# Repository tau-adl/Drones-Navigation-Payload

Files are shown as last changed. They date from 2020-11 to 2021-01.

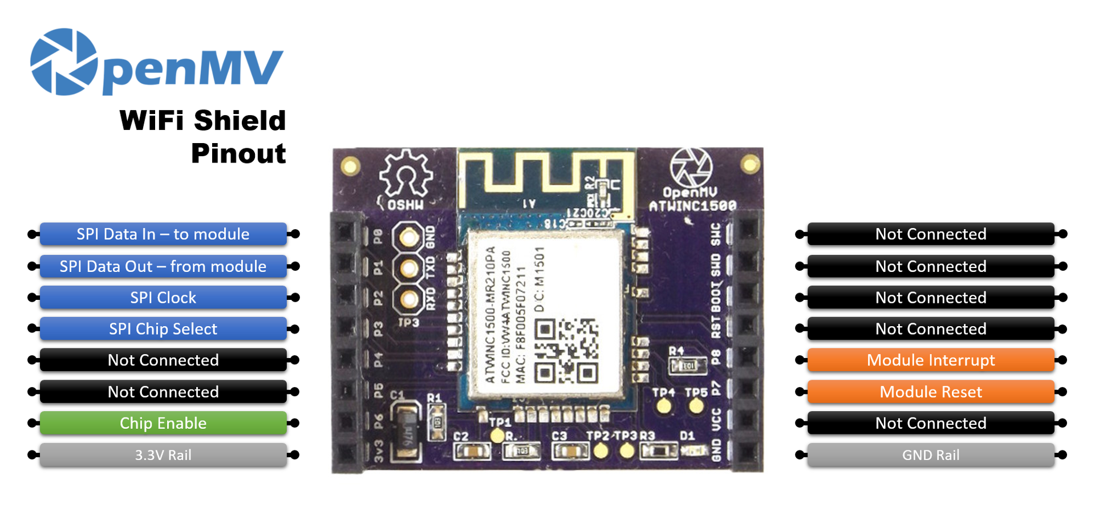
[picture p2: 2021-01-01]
datasheets/openmv/openmv-wifi-pinout.png

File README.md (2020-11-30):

# Drones-Navigation-Payload
The goal of the project is to build a payload taken by a drone that transmit both IMU and Images to a python script on a computer. 
Later, this information will be processed by ROS environment for navigation with SLAM algorithm. 

The Hardware for this project is based on the OpenMV(c) cH7 camera circuit loaded with global shutter camera, wifi shield and MPU6050 IMU sensor.

The repo cantains python script to be run as "ground-station" and the original firmware that runs on the main MCU.

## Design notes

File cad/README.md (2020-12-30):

# CAD files

## Hardware setup

## Dependencies

## Contributors and contributors
@Shenhavo
@danblana

case-r1.stl - OpenMV `https://github.com/openmv/openmv-boards/blob/master/cad/case-r1.stl`
OpenMV_Camera_Case - SteveTE `https://www.thingiverse.com/thing:1656029`

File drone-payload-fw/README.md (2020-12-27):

# drone-payload-fw

Project based on the OpenMV(c) firmware, modified to achieve real time image capturing and IMU data fusion, to be sent via Wifi to a  groundstation

## Hardware setup

** add circuit diagram **

|Part|OPENMV part|Model |
|--|--|--|
| MCU | OPENMVH7 | ST STM32H743 |
| Camera| OPENMV GS Camera  | ON MT9V034 |
| Wifi| OPENMV WifiShield | Atmel ATWINC1500 |
| IMU|  | Invensese MPU-6050 |
|Debugger/flasher||STlink V3|
|USB to UART|FTDI or similar|

## Debug info setup
uart @ baud = 115200.
win - `docklight` terminal or similar
ubuntu - `minicom`, `screen` or similar

# Defines and build configurations

- `camera_mngr.h` , frame size @  `FRAME_SIZE`,  `IMG_W`,  `IMG_H`
- `camera_mngr.h` , debug flags @  `CAMERA_BENCHMARK` - for printing acquisitions benchmarks,  `SAVE_INPUT_IMG_ON_SD`,  `SAVE_OUTPUT_IMG_ON_SD` - to save source and ouput images in SD card (~use carefully, it affects timings!)
- `main.h` - Wifi's SSID @ `MAIN_WLAN_SSID`

## Dependencies
STM32CubeIDE - Version: 1.4.2 - install from `https://www.st.com/en/development-tools/stm32cubeide.html`

## Contributors
@Shenhavo
@danblana

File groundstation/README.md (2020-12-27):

# groundstation

Ground station for `drone-payload-fw`
This code handles data comes from the drones payload, manages sockect and communication transactions utilizing proprietary protocol and exports the output on PC.

## Hardware setup

* wifi access
* drone payload with `drone-payload-fw` loaded
* tested on WIN10

## Dependencies
* numpy
* py-opencv
* opencv
* libopencv

if you use `ROS`
* ROS

## Contributors
@Shenhavo
@danblana

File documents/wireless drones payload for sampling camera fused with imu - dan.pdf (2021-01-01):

# אוניברסיטת תל אביב

הפקולטה להנדסת חשמל

## מטע"ד אלחוטי לרחפן לדגימת מצלמה וחיישן אינרציאלי בזמן אמת

## Real Time Wireless Drone’s Payload for

## Sampling Images and IMU data

פרויקט גמר לתואר שני בהנדסת חשמל

ע"י

# דן בלנארו

מנחה הפרויקט: מר יהונתן מנדל

המעבדה לרחפנים אוטונומיים באוניברסיטת תל-אביב

דצמבר 2020

## 1 תוכן עניינים

### 1 תוכן עניינים 2 |

### 1 מבוא 3 |

### 2 מטרות הפרויקט 4 |

### 3 איפיון דרישות המערכת 4 |

### 3.1 בחירת הרכיבים 4 | 3.2 סקר שוק 5 | 3.3 מצלמה6 | 3.4 חיישן IMU6 | 3.5 המודול האלחוטי 6 | 3.6 הבקר 7 | 3.7 חיבורים ואספקות מתחים 7 | 3.8 סקירת רכיבי הפרויקט 8 |

### 4 תכן מערכת 9 |

### 4.1 תרשים בלוקים: 9 |

10 | STMICRO STM32H743 - | הבקר | 4.2
11 | BOARD SUPPORT PACKAGE – GPIOS | והקצאת | BSP | 4.2.1
4.2.2 מפת חלוקת שעון מרכזי 13 |
4.2.3 פריפריות בשימוש 14 |
19 | ON SEMICONDUCTOR MT9V034 – | מצלמה | 4.3
20 | MICROCHIP ATSINC1500 - WIFI ה | מודול | 4.4
21 | INVENSENSE MPU6050 – IMU – | האינרציאלי | החיישן | 4.5

### 5.1 ארכיטקטורה 22 |

5.1.1 מבנה שכבות הקוד 22 |

### 5.2 תכנת תחנה קרקעית 25 | 5.3 ממשקי DEBUG, צריבה ושימוש במערכת 26 |

### 6.1 תצורת המדידה 27 | 6.2 תוצאות 27 |

### 7.1 סיכום 28 | 7.2 עבודות המשך 28 |

### 8.1 תמונת נוספות של המערכת 29 | 8.2 ביבליוגרפיה 30 |

## 1 מבוא

רחפנים כיום מנווטים באמצעות עיבוד החיישנים שמותקנים עליהם . אם עבור רחפנים בסביבות חיצוניות )outdoor ) משתמשים בחיישנים כגון GPS, הרי שלרחפנים בסביבות סגורות )Indoor )לא ניתן לשתמש בחיישן כזה.

הפרויקט עוסק במימוש מטע"ד )payload )אלחוטי וקומפקטי לרחפן, למטרות חישה ודגימה של רכיבים לטיוב הניווט באמצעות אלגוריתם SLAM.

לטובת הנ"ל, ניתן להשתמש בחיישני עזר נוספים, כגון מצלמה - להתמצאות במרחב, ובחיישנים אינרציאליים )IMU)- שיכול להשלים מידע לאלגוריתמי עיבוד תמונה בנוגע למהירות התנועה וקצב התנועה של הרחפן. באמצעות היתוך מידע בין 2 החיישנים, ניתן להשיג מידע חזותי-אינרציאלי ולבצע מיפוי והתמצאות של המרחב )SLAM(

]1[

רחפנים שמסוגלים לנווט בסביבה סגורה יכולים להביא תועלת רבה במקום שבה רחפנים לסביבות חיצוניות מביאים – לדוגמא ליישומי בנייה, חקלאות, רפואי, מסחרי, צבאי, קולנוע וגם לפנאי.

העבודה כאן מציגה שיתוף פעולה במעבדה לרחפנים אוטונומיים באוניברסיטת תל אביב ADL-TAU, על מנת לממש את מטרות הפרויקט
- סקר ספרות
- הבנת דרישות המערכת
- תכן על
- סקר שוק ובחירת רכיבים
- מימוש החומרה והתכנה לפרויקט
- חקר ביצועים
- סיכום

## 2 מטרות הפרויקט

הפרויקט יממש מערכת לחילוץ מידע חזותי-אינרציאלי )inertial visual )מהחיישנים במטע"ד קטן, תחת הדרישות הבאו: .1 גודל קטן
.2 צריכת זרם מינימלית
.3 תקשורת באמצעים סטנדרטיים לתחנת קרקע – .etc dongles MHz900 ,BT ,Wifi .4 שליחת המידע עם חותמות זמן ברזולוציה של כ msec1 .4.1 מדיד אינרצילי IMU ב6 צירים - תאוצה קווית בצירים z ,y ,x, תאוצה זוויתית בצירים z ,y ,x .4.2 תמונה ממצלמה )RGB / Grayscale – )בקצב FPS20 .4.3 המידע יישלח בשיהוי של כ msec150 .5 אפשרות להריץ את תחנת הקרקע ע"ג PC עם מערכת הפעלה 18.04 Ubuntu .6 שמירת המידע בתיקיה ייעודית על מנת לחבר אח"כ את תוצרי המערכת לסביבת ROS

## 3 איפיון דרישות המערכת

### 3.1 בחירת הרכיבים

עלינו לבחור אריכטקטורה שתאפשר מימוש גמיש ויעיל מבחינת משאבים של דרישות הפרויקט. המערכת תורכב מתחנת קרקע, וממטע"ד שיותקן על הרחפן. בצד הבית לרשותנו מחשב PC, עם תקשורות אלחוטיות סטנדרטיות )Wifi ,Bluetooth). אילוץ התקשורת הנחה בבחירת הרכיבים למטע"ד.

למטע"ד נבחר יחידת עיבוד מרכזית )CPU )שתנהל את לוגיקת דגימת החיישנים – מצלמה, מדיד אינרציאלי, תתזמן את דגימתם ותנהל את לוגיקת התקשורת האלחוטית. הדרישה ליחידות המטע"ד הינה שימוש ברכיבים סטנדרטיים מבחינת Market To Time, היתכנות מענה לאילוצי המערכת, יכולות debug גבוהות ותמיכה בקהילות פיתוח עם עדיפות לתשתיות קוד-פתוח.

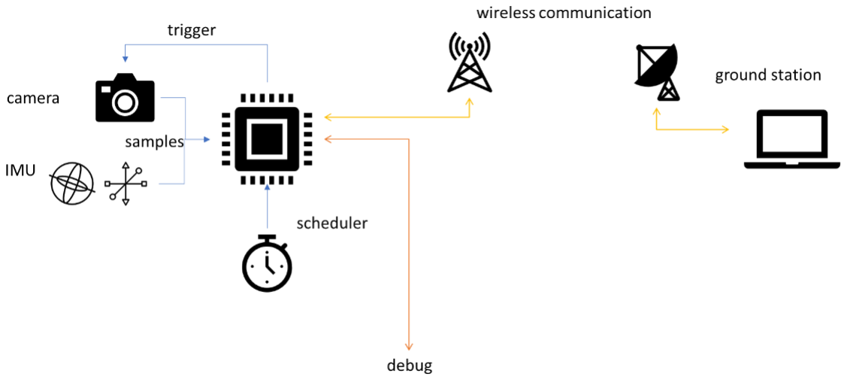
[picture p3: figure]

### 3.2 סקרשוק

טרם תהליך הפיתוח ערכתי סקר שוק על תשתיות ומוצרים שיתנו מענה לדרישות הפרויקט, אסכם כאן את החומרות שמצאתי ואת יתרונן וחסרונן למימוש המשימה.

לסיכום, נבחרה חומרת 7H OpenMV, שאפרט את תהליך התאמת החומרה למשימה בהמשך.

model | features | Pros | Cons
Bitcraze Crazyflie 2.1 | Small scale drone hardware with wireless communication and programming capabilities. Contains IMU on board. STM32F405 MCU (Cortex-M4, 168MHz, 192kb SRAM) | Small scale factor, open-source community | Not exporting I/F for external camera. The Bluetooth comm might be a little bit slow for our application.
3DR Pixhawk | 3 IMU on board, wireless communication is based on ESP32 module (Wifi) STM32F427 MCU (Cortex-M4, 180MHz, 256kb SRAM) | The hardware is versatile, open-source repo is well maintained | No JTAG interface for real time debug No dedicated digital camera I/F. Not compact.
Beagle Bone Blue | Board conaining an cortex a8, comm interfaces alongside Wifi & BT OSD3358 (TI Cortex-A8 512MB DDR). No IMU on board. | Versatile, open-source, heavy lifter. No dedicated I/F for camera – a USB camera can be used with proper drivers | The use of an embedded Linux OS might be a little
ESP32 Camera Module Development Board (OV2640) | An ESP8266 based board (160MHz, 160KB RAM) Has Wifi integrated! But the debug interfaces might be difficult! | Open-source, the wifi is built into the MCU. | No dedicated camera port, utilizing an SPI might be slow for this application. The use of SPI camera might be a limitation for future design. Debug interface is not convenient for real-time debug
OpenMV H7 | Open-source small scale factor hardware and firmware. A product dedicated for image processing applications. User can utilize the hardware as the product is built as shileds (IMU, Wireless communication, Camera) | Contains versatile hardware and cameras. Well maintained user forums and repo | Not all MCU’s GPIOs are available to the user via standard headers.

### 3.3 מצלמה

בחרנו מצלמת CMOS עם חשיפה של Shutter Global, על מנת להבטיח חשיפה אחידה של כל שורות הפיקסלים. השיקול נבע מהתאמת המצלמה לרחפן - פלטפורמה שזזה במהירות, והימנעות ממריחות בתמונה בזמן החשיפה, כמו הדוגמא בתמונה הבאה:

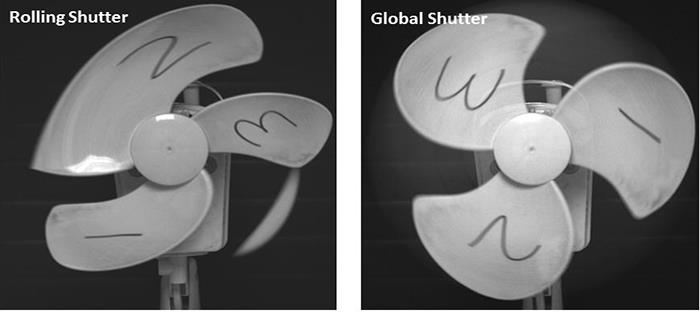
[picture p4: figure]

Figure1 : rolling vs. global shutter

למצלמה יש חיישן בגודל inch1/3 עם רזולוציה מקסימלית של עד 480x752 פיקסלים, יכולת להפיק fps60 ברזלוציה מקסימלית, עם רזולציה של bit10לפיקסל בגווני אפור. כמו כן, המצלמה מנגישה רגל strobe על מנת לאפשר לבקר לתזמן את רגע לכידת התמונה ובכך להבטיח את עדכניות התמונה.

המצלמה מאפשר אפשרות לחשיפה אוטומטית, וזה המצב שבו עבדנו, עם קצב שעון מקסימלי של MHz.27

נפחי פלט התמונה ישמשו אותנו בבחירת תצורת המערכת, מבחינת רזולוציה ו fps מובאים להלן:

Resolution | width | height | fps | Mbit/sec
Full resolution | 752 | 480 | 20 | 57.8
QVGA | 320 | 240 | 20 | 12.3

### 3.4 חיישן IMU

נבחר רכיב לדגימת תאוצות ב6 צירים )3 רכיבי תאוצה בצירים ליניאריים ו3 רכיבי תאוצה בכיוון סיבובי(. רכיבי התאוצה יאפשרו לאלגוריתם העיבוד על תחנת הקרקע, להבין תנועות יחסיות של הרחפן, ולטייב את עקיבת התמונה.

רזולוציות דגימה אופייניות של הרחפן תהיה כ dps250 לתאוצה סיבובות, וכ g+/-2לתאוצה קווית עבור כל ציר.

### 3.5 המודול האלחוטי

על המודול האלחוטי להיות בעל פרוטוקול תקשורת סטנדרטי לPC( Wifi/ Bluetooh), עם ממשק תקשורת סריאלי לבקר המנהל.

נבחר לממש את התקשורת ע"ב Wifi בגלל יתרונות רוחב הסרט, פשטות החיבור אליו והיכולת העתידית לאגור מידע ממספר מטע"דים בו-זמנית ע"י התחברות של מספר מטע"דים לאותו Point Access.

המודול האלחוטי צריך להתחבר לתחנה קרקעית ע"ג PC, לקבל ולשלוח את המידע מצד המטע"ד.

### 3.6 הבקר

לבקר יש מספר משימות באפליקציה שלנו:

- ניהול החיישנים והגדרותיהם
- סנכרון זמן דגימת החיישנים
- ניהול פרוטוקול תקשורת שמוצמדת אליו חותמת זמן
- ניהול תקשורת אלחוטית עם תחנת הקרקע
- ריכוז המידע מהחיישנים, ודחיסתו
- קיום ממשקי תקשורת ס ממשקי תקשורת C2I /SPI לחיישנים, UART לצורך הודעות debug למשתמש
- ממשק JTAG/SWD לצריבה ודיבוג של התכנה בזמן אמת
- יש יתרון לבקר עם ממשק תקשורת סטנדרטי למצלמה, דוגמת LVDS או ממשק מקבילי

לבקר צריכים להיות ממשקי תקשורת שמתאימים לרכיבים שנבחרו, ויכולת לתת חותמת זמן לכל מידע שמגיע מהחיישנים, לטובת עיבוד המשך בתחנת הקרקע.

מכיוון שמערכת הפעלה מוסיפה עוד תקורה בנפח הקוד, בריצה ובזמן ניהול האירועים שלה, ועל מנת לאפשר פיתוח מהיר ואמין, עם מעטפת ביצועים time real, נבחר לממש את האפליקציה ללא מערכת הפעלה, אלא בכתיבה של התכנה -bare metal לבקר.

### 3.7 חיבורים ואספקות מתחים

למערכת צריכה להיות אפשרות להיות מוזנת ממתחים סטנדרטיים, לדוגמת סוללת V3.7 Lipo, או מחיבור USB של V.5

### 3.8 סקירת רכיבי הפרויקט

מודול ה7H OpenMV נותן לנו מענה חומרתי לרוב דרישות הפרויקט, ובפרק הבא נסקור את השינויים שבוצעו במודולים הקיימים על מנת לתת מענה מיטבי לפרויקט.

כל רכיבי המערכת עמידים לעבודה בטמפרטורת חדר, ) C° +70 to -20). ניתן לראות גם לפי התמונות שהם בנויים בצורת shields שיאפשרו ממשק נוח לחיבור בין החלקים השונים.

לנ"ל שידכנו צורב מדגם 3v stlink של חברת STmicro – שנתן לנו ממשק JTAG וחיבור UART למטרות דיבאג במערכת.

Part | Model | Description | Size | Weight
MCU | STmicro STM32H743 | Implements mi-cropython, in-cludes DCMI I/F, RGB LED, up to 480MHz Idd = 170mA @ 3.3V Regulator – up to 5.5v, 1A | 45x36x30mm Incl. camera | 19gr
Camera | ON MT9V034 | HFOV = 70.8° VFOV = 55.6° Idd = 200mA max | 35x25x28mm | 10gr
IMU | Invensense MPU6050 | Idd <4mA | 20x25x7mm | ?

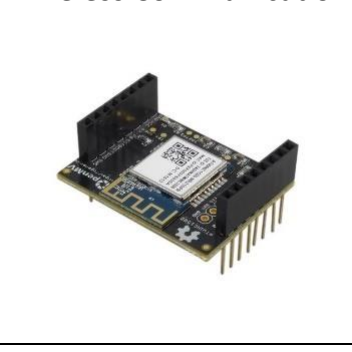
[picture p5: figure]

Wireless Communication | Microchip AT-winc1500 | Up to 12.5Mbps Idd =100 mA @ 3.3V | 36x27x20mm | 7g

## 4 תכן מערכת

נציג את בחירת הפרמטרים ונקודות העבודה לכל מודול כמו גם הממשקים בין הרכיבים השונים שמביאים נקודת עבודה אופטימלית לבעית הפרויקט.

### 4.1 תרשים בלוקים:

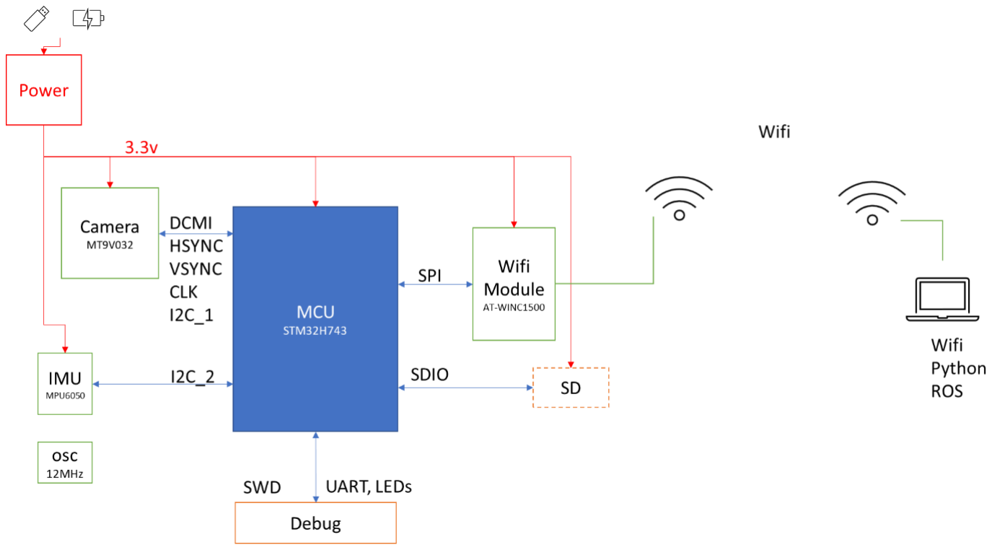
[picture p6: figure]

Figure:2 block diagram

יחידת אספקת המתחים מייצבת מתח V3.3 לצרכנים במעגל. ניתן להזין את המעגל באמצעות USB או סוללה חיצונית.

הבקר מקבל שעון ממתנד חיצוני של MHz12 לצורך הריצה שלו. כמו כן, הבקר מתחבר דרך ממשקי תקשורת שונים לצרכנים במעגל-

למודול ה Wifi ממומש חיבור תקשורת SPI תקני )CS ,CLK ,MOSI ,MISO).

למודול ה IMU מתחברים באמצעות /C2I

הממשק למצלמה כולל bus - ממשק מקבילי ברוחב 8 ביט, שנקרא DCMI, כמו גם קווי סינכרון לתחילת קליטה של שורה/עמודה חדשה, אות שעון למצלמה, וממשק C2I לקינפוג ושינוי פרמטרים במצלמה.

STMICRO STM32H743 - | הבקר | 4.2
הבקר משמש אותנו להגדרת הפריפריות במעגל לנק' העבודה הרלוונטית, התקשורת ביניהן, תזמון האירועים, ניהול הפרוטוקול וניהול של המידע הנאגר.

לבקר יש אילוצי זכרון RAM, כאשר בהתמודדות עם תפיסה של מטריצות פיקסלים גדולות, הופכים להיות מגבלת מערכת שיש להתמודד איתה בהיבט האפליקציה. כמו כן מניתוח של בעית זמן השליחה, רוחב הסרט הנתון והקצבים שהתבקשנו לעמוד בהם, הבנו שעלינו לממש דחיסה לתמונה, לכן מימשנו כאן דוחס jpegכפי שיפורט בפרקי המימוש בהמשך.

תכן הלוגיקה והעיבוד של הבקר, צריכים להתכנס מבחינת ציר הזמן לצילום, דגימה, עיבוד ושליחה לתחנה הקרקעית – על מנת לעמוד בדרישות הפרויקט של צילום ושליחה בtime real. לצד כל חלק נסקור את הזמן האופייני שלוקח לכל חלק ונחשב את תקציב הזמנים.
ca_mi - משך הזמן לחשיפת חיישן המצלמה והעברת התמונה לבקר |
moc_mi - משך הזמן לדחיסת התמונה |
mi - משך הזמן לקבלת מידע מהחיישן האינגרציאלי |
moc - משך הזמן לשליחת המידע |

להלן דיאגרמת בלוקים של פריפריות הבקר, גישות הזכרון והממשקים האפשריים לBSP.

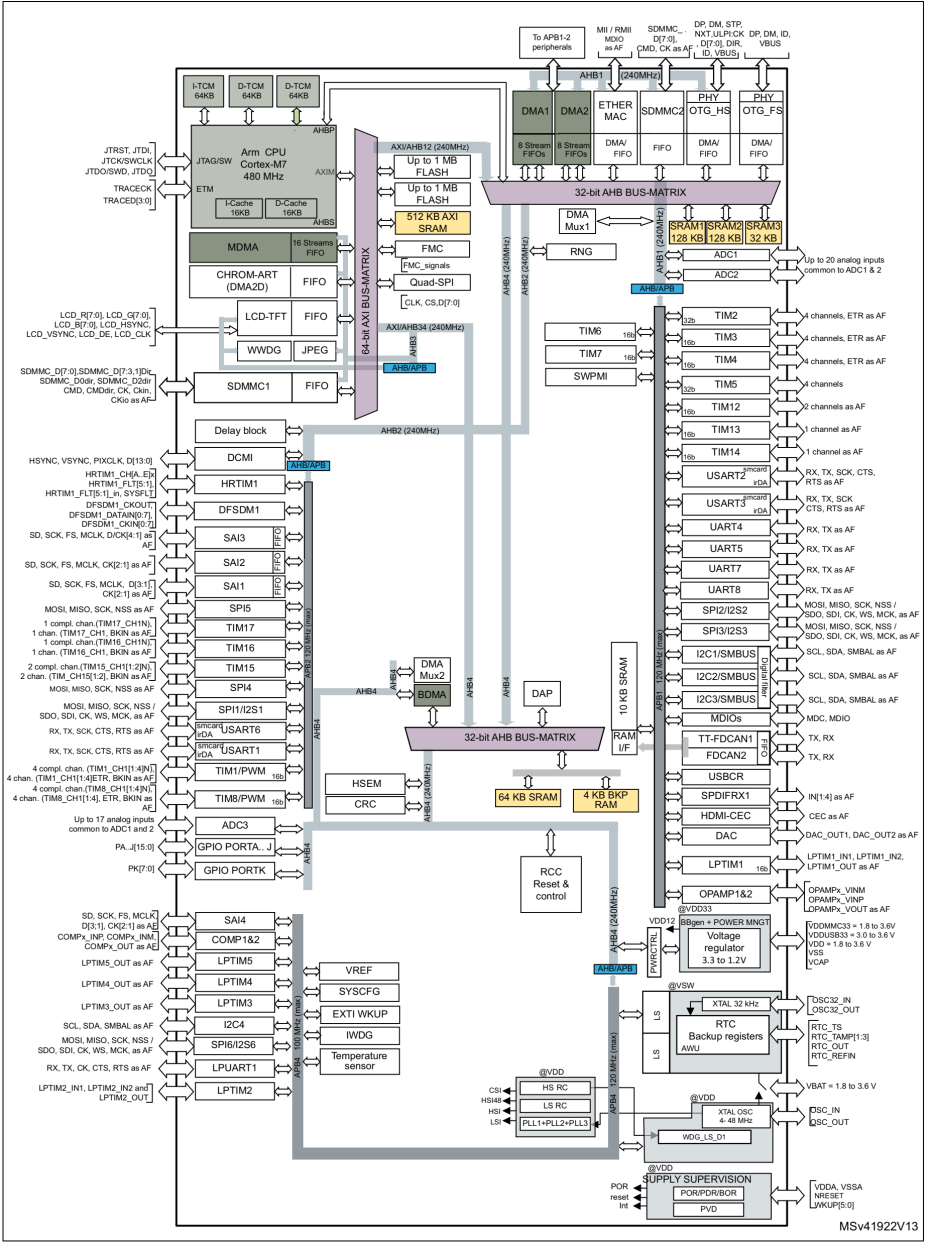
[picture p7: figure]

Figure :3 STM32H743 block diagram

Board Support Package – GPIOs | והקצאת | BSP | 4.2.1
להלן הpinout שבחרנו למימוש הבקר ולהקצאת ה Output/Input Purpose General – GPIO.

הממשקים החשמליים )אספקות ואדמות(- הם אילוץ במימוש, ושאר ה pinout אליו צריכים להתכנס אליו לפי שרטוטי ה schematicsשל חומרת ה OpenMV, מפורט בתמונה הבאה.

כמו כן,התוספת של חיישן הIMU דרך חיבורי הheader, אילצה אותנו לפרוס קווים נוספים לטובת UART, באמצעות הלחמה של wire maget ע"ג רגלי הבקר, באופן שיאפשר שימוש במקביל גם בממשק ה debug של ה UART וגם על מנת לתקשר עם רכיב הIMU. הלחמת קווי התקשורת בוצעה על רגלי הבקר 23) 1PA ,)22 (0PA, בנוסף לחיבור קו אדמה לטובת התקשורת.

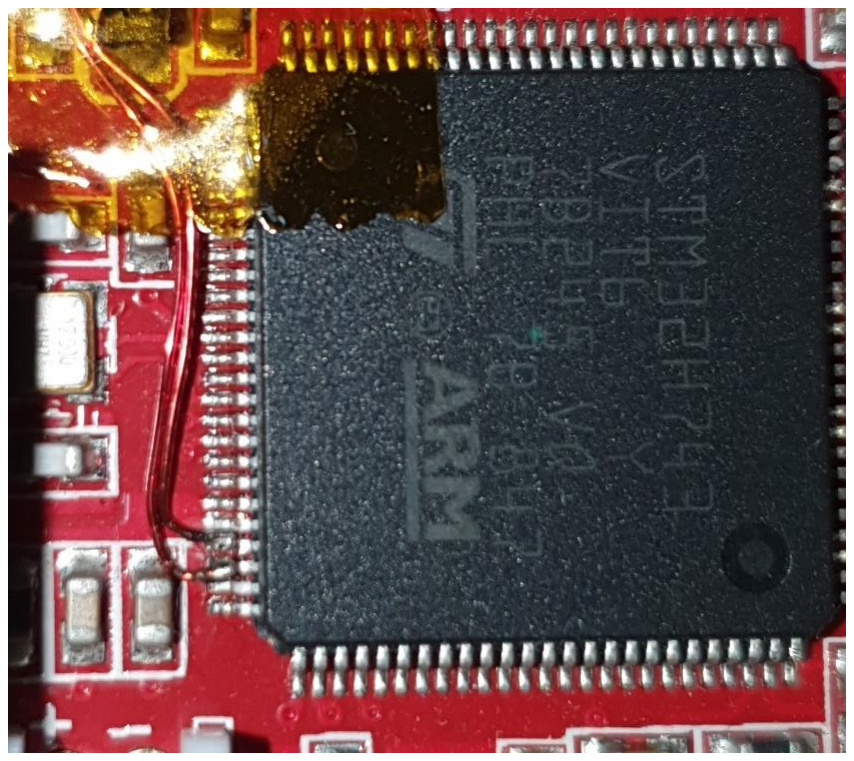
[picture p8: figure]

Figure :4 Debug UART wiring

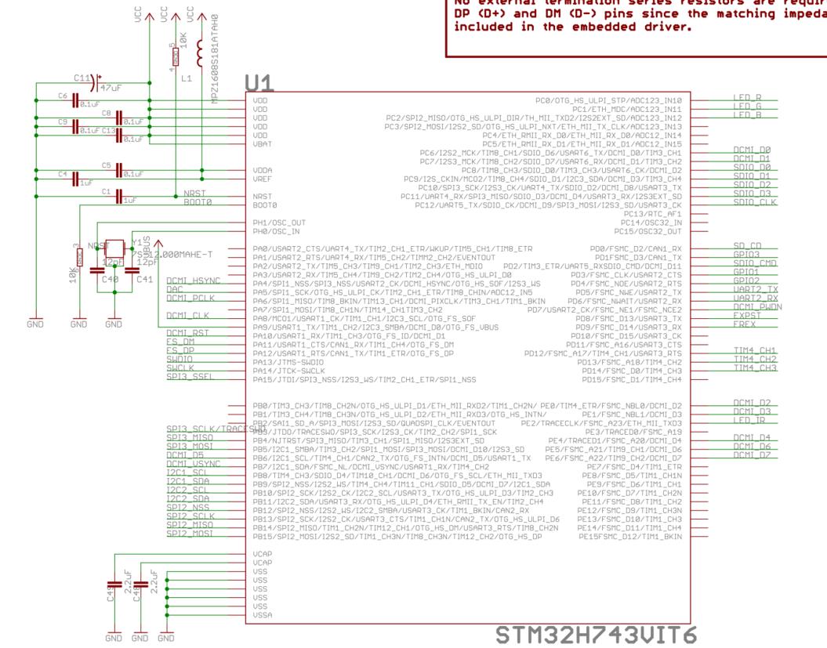
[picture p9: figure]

Figure5 : OpenMV H7 (c) schematics

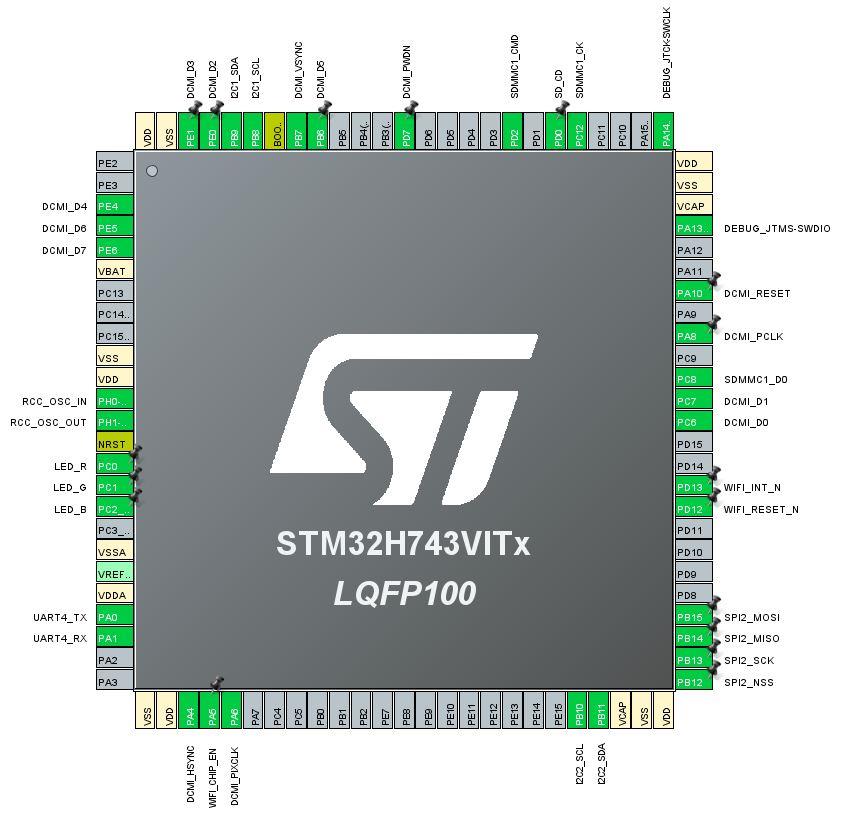
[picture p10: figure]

Figure6 : STM32H7 pinout

### 4.2.2 מפת חלוקת שעון מרכזי

באמצעות סביבת ה CubeMx הגדרנו את חלוקת השעונים לחלקי הבקר. בגלל סיבות שיפורטו בהמשך, השתמשנו במכפילי שעון ומחלקים כדי לעבוד בקצב העבודה המקסימלי שהבקר מאפשר – MHz.480

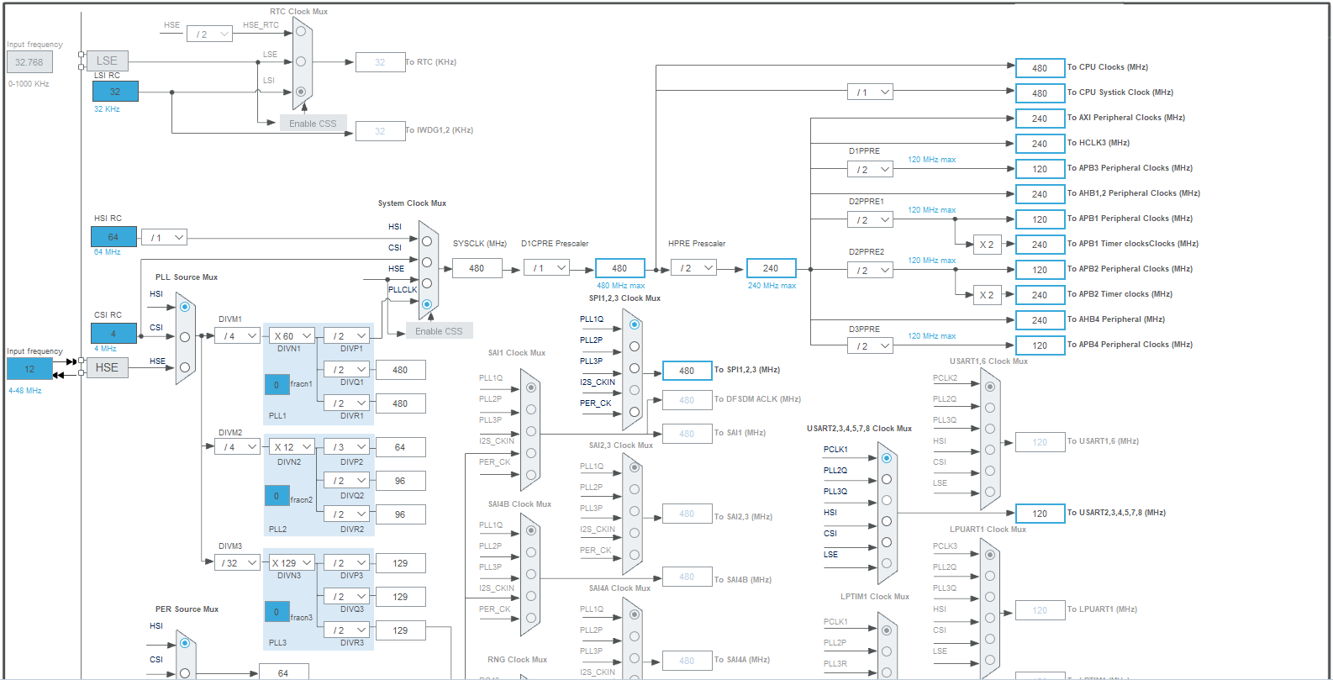
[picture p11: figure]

Figure7 : CPU clocks regime

### 4.2.3 פריפריות בשימוש

להלן ניצול משאבי הבקר

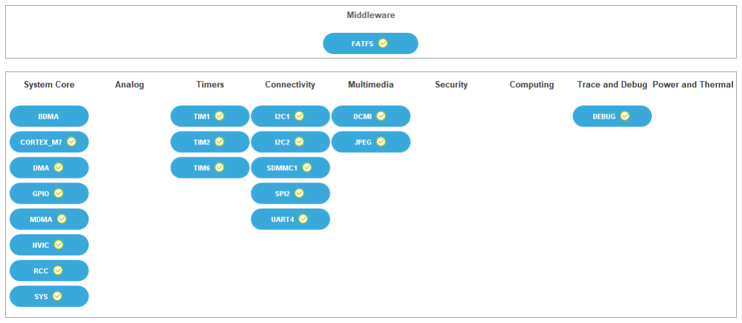
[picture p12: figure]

Figure 8 : CPU peripherals

MDMA /DMA 4.2.3.1
זוהי פריפרייה שמאפשרת גישת זכרון ישירה בין אזורי זכרון שונים בבקר, עם העברת מידע בכלי חומרתי, שאינו מעכב את ריצת התכנה. באפליקציה שלנו - מוגדר כגישה ישירה בין זכרון פריפריית תפיסת המצלמה )DCMI )לזכרון הRAM, כמו כן בין הRAM לפריפריית דוחס התמונות.

היכולת הזו מאפשרת לבקר לתקשר במהירות וביעילות ולקבל מידע מהפרירפיות השונות שמפורטות כאן, מבלי לעכב באופן משמעותי את התכנה.
לדוגמא – דחיסת התמונה לפורמט JPEG ממומשת אצלנו ע"י העברת 2 שורות בכל פעם לפריפריית הדחיסה חומרתית והמתנה לביצוע עיבוד הפריפרייה. כאשר הפריפרייה מסיימת את החישוב והדחיסה על 2 השורות, היא מעבירה באמצעות הDMA את המידע למרחב הזכרון ב(Memory Access Random (RAM שהוגדר בבקר להמשך העבודה, הבקר מקבל פסיקה )interrupt )ובכך מקבל טריגר להמשיך להעביר את נתח התמונה הבא לעיבוד הפריפרייה החומרתית וכך חוזר חלילה, עד לסיום הדחיסה.

עוד שימוש לDMA אצלנו, הוא להעברת המידע מהמצלמה לזכרון הבקר.

Cache and MPU 4.2.3.2
לטובת תקשורת והעברת מידע בין אזורי זכרון שונים, הוגדרה גישה מותרת לאזורי זכרון בהתאם להגדרות הDCMI וה JPEG לפי אילוצי הבקר.

JPEG Encoder 4.2.3.3
כפי שתואר בפרקים הקודמים, דרישות הפרויקט שמבקשות תמונה ברזולוציה טובה דיה )נניח 240x320), בקצב של fps,20 מאלצת רוחב סרט גדול מאוד של כMbps12~. מאוחר יותר, התברר שהרוחב סרט האפקטיבי שמצליחים להוציא מרכיב התקשורת האלחוטית הוא כMbps,3 עובדה שהפכה את השימוש בדוחס להכרח.

הפרמטרים לדוחס התמונה מאפשרים שימוש במרחב צבעים שונה להלן דוגמא של תמונה שנדחסה באמצעות פריפריית הדוחס החומרתית שבבקר, תחת אילוצי השימוש שבה:

Parameter | Value
JPEG_RGB_FORMAT | JPEG_RGB888
JPEG_CHROMA_SAMPLING | JPEG_420_SUBSAMPLING
JPEG_YCBCR_COLORSPACE | JPEG_COLOR_SPACE
JPEG_IMAGE_QUALITY | variable
W | 400 | 400 | 400
H | 240 | 240 | 240
Size | 281KB | 10.8KB | 64.2KB
Q | - | 75 | 100
Size factor | 1 | 0.0384 | 0.228
ניתן לראות שאפשר להקטין את התמונה, מבלי לאבד איכות באופן ניכר, בפקטור 0.04~ ביחס לנפח המקורי. הקטנת נפח התמונה, תאפשר להעביר תמונה ב latency נמוך ומבלי לפתוח הרבה נפח.

מבחינת לוח הזמנים לעיבוד, עבור גודל תמונה 480x,640 לפי דפי הנתונים יש לקחת msec62 timg_comp = בתקציב הזמנים.

להלן תיאור תהליך דחיסת התמונה בפריפרייה החומרתית שבבקר:

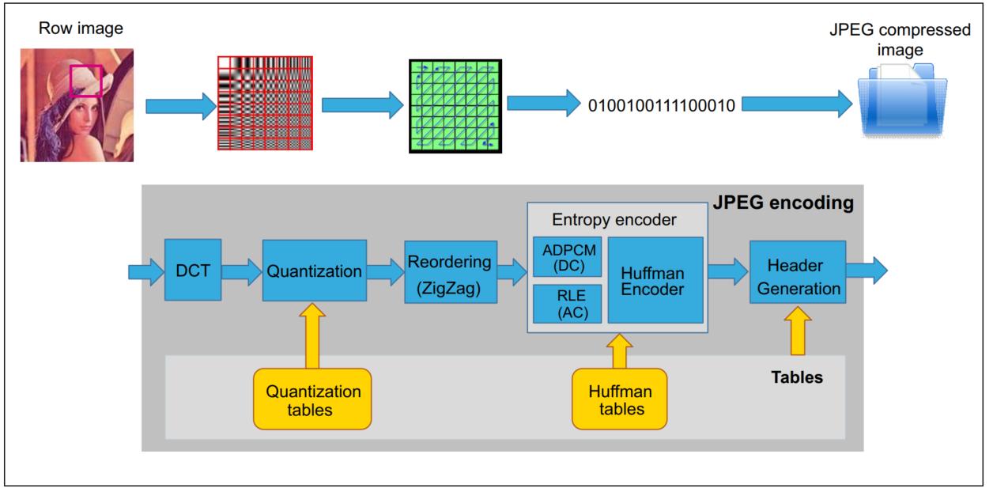
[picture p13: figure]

Figure9 : JPEG encoding flow

מהלך הדחיסה בנוי מקבלת מפת ביטים שלמה של התמונה )לדוג' 240*320 פיקסלים(, ולאחר מכן קריצה של חלקים מהתמונה והעברתם לדוחס – 16 שורות בכל פעם, המרתם למרחב צבעים YCbCr וליחידות המרה מינימליות )MCU )לטובת דחיסה )DCT, קוונטיזציה, קידוד אנטרופיה, קידוד Huffman), וייצוג קובץ הjpeg המתאים.

תהליך הקריצה, הגדרת הפרמטרים לדוחס, וטיפול הפלט הדוחס הם בצד התכנה. תהליך הדחיסה עצמו וההמרה מתבצע באופן חומרתי.

Timers 4.2.3.4
1TIM – שעון המצלמה,במצב עבודה של OC( מייחצן אות שעון ע"ג רגל מוגדרת בבקר, כקלט למצלמה( לתדר MHz.25

2TIM – שעון זמן הדגימה לחיישן ה IMU - מכוון זמן מחזור msec1( kHz1).

6TIM – ש עון זמן ניהול השליחה למודול ה Wifi - מכוון זמן מחזור msec0.25( kHz4).

UART 4.2.3.5
משמש אותנו למטרת תקשורת סריאלית בין המחשב ול debug של המערכת - ממשק הודעות טקסטואליות שמוצמת לחותמת זמן לטובת חקר ביצועים של המערכת. מוגדר להיות בקצבbps115,200 . ממשק ה debug יומחש בפרק ביצועי המערכת.

SPI 4.2.3.6
2SPI – למודול ה Wifi, בקצב MHz60[ הערה: הקצב הזה חורג מהקצב המומלץ של היצרן, שהוא עד MHz48 ]

Digital Camera Interface – DCMI 4.2.3.7 הבקר מכיל ממשק למצלמה על מנת לתקשר עם מצלמות חיישני CMOS באמצעות bus ברוחב bit8-14 על מנת לקבל וידאו. הפריפריה מאחדת את הממשק והפרוטוקל לתזמון הפיסלים ביחס לאות השעון PIXCLK שיוצא מהחיישן, כמו גם סנכרון לאותות סימון השורות-עמודות של הframe, שקרויים VSYNC ו – HSYNC בהתאמה.

הממשק למצלמה באופן כללי, מורכב מ:

- קווי שליטה למצלמה )טריגרגים, reset )
- קווי מידע ותקשורת מחיישן המצלמה )המידע מחיישן הADC שדוגם את הפיקסלים(. הסבר על הפרוטוקול מפורט בפרק המצלמה.
- קווי תקשורת להגדרת פרמטרים לעבודת המצלמה )זמן חשיפה, רזולוציה(

אצלנו הממשק מוגדר ברוחב bit,8 עם סנכרון מצד הבקר. עם מימוש העברת הframe באמצעות 2DMA.

השימוש בDMA מאפשר לבקר להעביר את המידע מפריפריית הDCMI למרחב הזכרון שמבצע עיבוד על התמונה. פריפריית הDCMI נמצאת שייך ל2AHB, יחד עם 2DMA + 1DMA. על מנת להעביר את המידע לאזור הזכרון בו רצה האפליקציה ב – SRAM-AXI, ע לינו להגדיר (Unit Protection Memory (MPU עם הרשאה לגישה בין אזורי הזכרון הנ"ל. זמן החשיפה האופייני של מצלמה )msec16 )~וזמן השליפה של המידע מהמצלמה הוא זניח
. | ומסתכם בכ-

img_acq~16.7msec

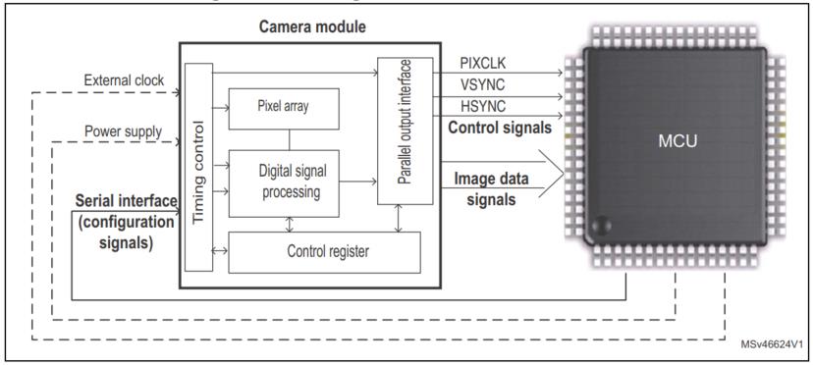
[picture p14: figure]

Figure10 : MCU-Camera DCMI I/F

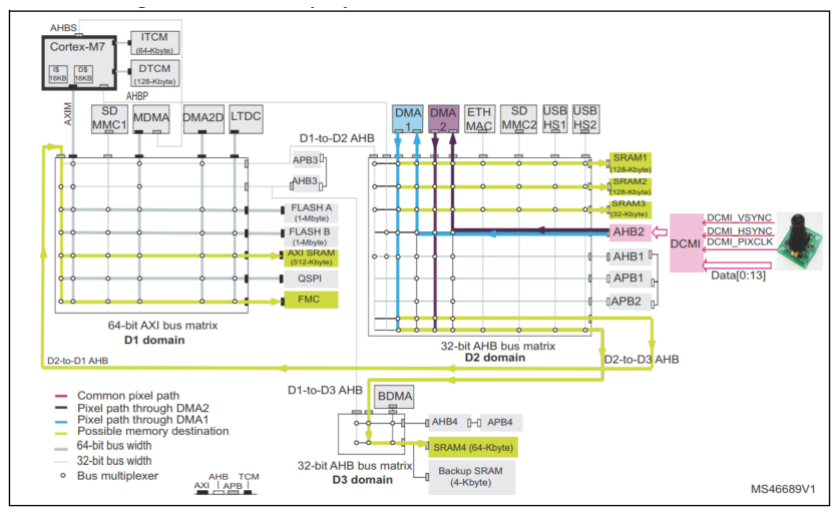
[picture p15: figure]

Figure11 : DCMI memory access

פלט התמונה שנשמר מהמצלמה, הינו מפת ביטים )bitmap), לפי גודל התמונה שהוגדר, כאשר כל פיקסל בגוון אפור בגודל bit8 לפיקסל. התמונה תישמר בבאפר במרחב הSRAM_AXI שיוקצה מראש לגודל התמונה הרצוי. המצלמה אצלנו הוגדרה לרזולוציית תמונה של 240X320 פיקסלים.

I2C 4.2.3.8
1C2I – עבור מודול המצלמה, בקצב KHz400
400KHz | בקצב | ,IMUה | לחיישן | – I2C2
SD + FATFS | 4.2.3.9
למטרות debug וחקר ביצועים, הושמש ממשק לשמירת פלטי המצלמה והדחיסה ע"ג כרטיס SD במערכת קבצים FATFS. השימוש בפיצ'ר הנ"ל אפשרי באמצעות הדלקת דגל בקימפול הקוד – בקובץ h.mngr_camera - אפשור ה define של
על | בהתאמה | והפלט | הקלט | תמונה | שמירת | את | יאפשרו | SAVE_OUTPUT_IMG_ON_SD - ו | SAVE_INPUT_IMG_ON_SD
כרטיס הSD. לשים לב שהפעולות הנ"ל יכולות להשפיע על קצב עיבוד ושליחת הנתונים, לכן יש לעדכנם בהתאם. כמו כן, יש לפתוח את פלט ה bmp שנשמר באמצעות סקריפט קצר בpy.plot2_raw .

ON SEMICONDUCTOR MT9V034 – | מצלמה | 4.3
המצלמה שבשימוש אצלנו היא מצלמת Shutter Global עם חיישן CMOS בגודל inch.1/3 כמו כן, תת הדגם שאנחנו עובדים איתו מכיל רזולוציה של עד 480 x752 בגווני אפור עם רזולציה של bit10 דגימת ADC לפיקסל.

ממש המצלמה מובנה באמצעות פריסת המעגל של OpenMV וממומש לפי הדרישה בדפי הנתונים.

רגלי הSDATA/SCLK מחווטות לרגלי 1C2I של הבקר. רגלי ה SYSCLK מחווטת לאות שעון שהבקר מייצר )בתדר MHz25), כאשר המצלמה תומכת באות שעון עד MHz.27

ממשק ה Exposure מאפשר שליטה על חשיפת החיישן של המצלמה, אולם לא מימשנו אותו כאן במערכת )ניתן לממש אותו ע"י הגדרת רגל 4PB בבקר וניהול החשיפה ביחס לתפיסת התמונה.

רזולוצית המצלמה נקבעה מטעמי זכרון וקצבים – להיות על (QVGA (240x.320

הממשק המקבילי של פלט המצלמה – (9:0) Dout נכנס לרגלי ה DCMI שהוגדרו בבקר כאשר מטעמי חומרה ואינטגרציה, ממומשים בפועל רק bit8 של התקשורת, קרי (9:2)Dout. פרוטוקול העברת המידע בין החיישן למצלמה מפורט בתמונה בהמשך.

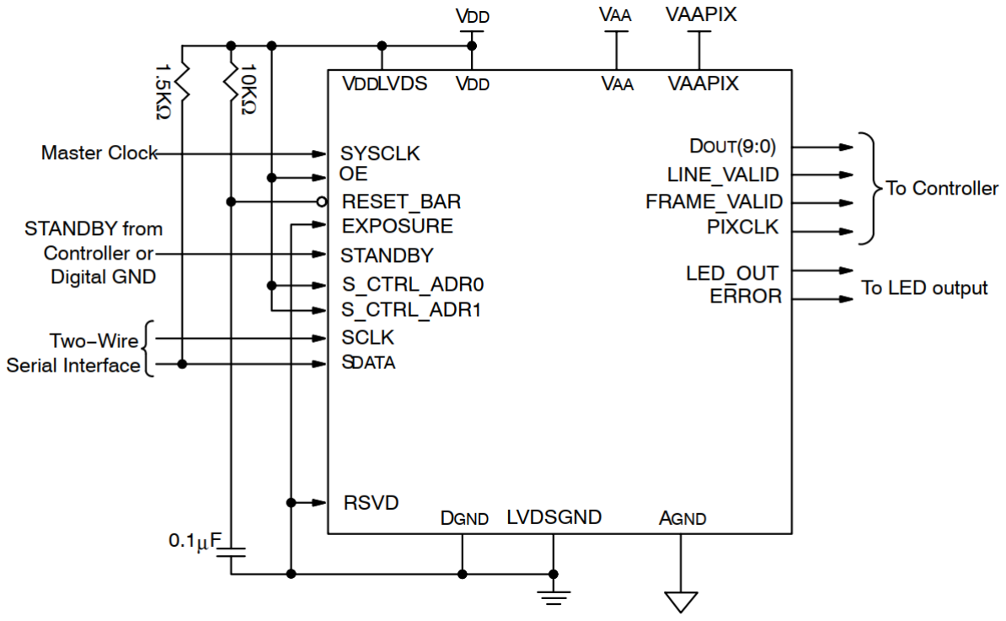
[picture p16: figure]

Figure12 : MT9034V pinout

Figure 13 : Pixel data protocol

MICROCHIP ATSINC1500 - WIFI ה | מודול | 4.4
מודול ה Wifi מאפשר לנו לקיים תקשורת עם כל מודם Wifi סטנדרטי, במצבי עבודה של (STA (Client או (AP (Host.

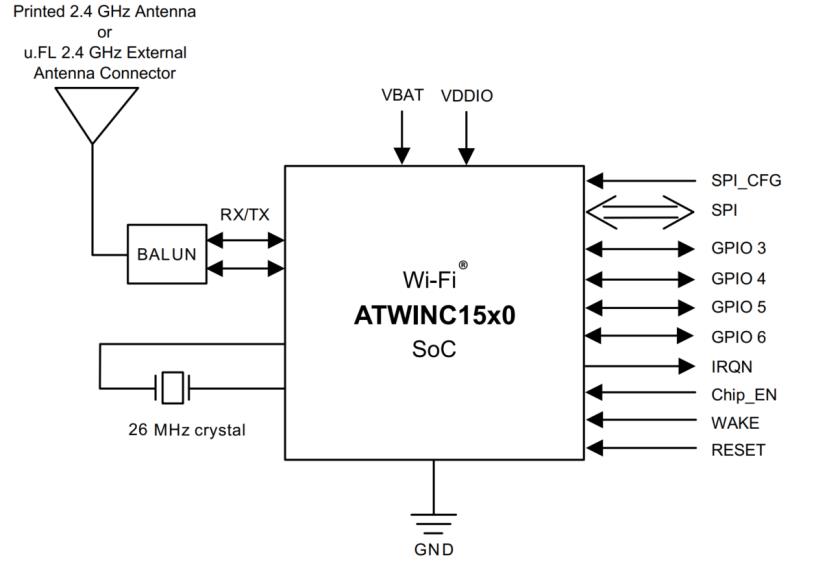
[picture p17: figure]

Figure 14 : ATWinc1500 diagram

Feature | Value
WLAN standard | 802.11b/g/n
Host interface | SPI, 28MHz max
Data rate | 802.11b: 1, 2, 5.5, 11Mbps 802.11g: 6, 9, 12, 18, 24, 36, 48, 54Mbps
Sensitivity | -76dBm @ 802.11g 48Mbps OFDM
Output power | 18.5dBm max @802.11b 11Mbps
Power consumption | Ivbatt = 268mA, Ivddio = 22mA max @802.11g

### 4.4.1.1 ביצועי המודול

מהעבודה של השותף שלי לחלק השני של הפרויקט, נמדד כי הביצועים האפקטיביים של המודול הינם כ Mbps.3 עובדה שהפכה את עבודה הדחיסה להכרח, כמו כן, אילצה את גודל התמונה האפקטיבי שאנחנו יכולים לעבוד איתו, להספיק מבחינת תקציב הזמן לדחוס ולשלוח, כאמור 240X320 פיקסלים.

INVENSENSE MPU6050 – IMU – | האינרציאלי | החיישן | 4.5
החיישן נועד להקליט תאוצות לינאריות וסיבוביות של הרחפן. החיישן הזה מציג ביצועים טובים מבחינת טווח דגימה וצריכות זרמים. כמו כן, חיפשנו רכיב עם דרייברים ותמיכה ברשת, שאכן הרכיב הזה עומד פרמטר.

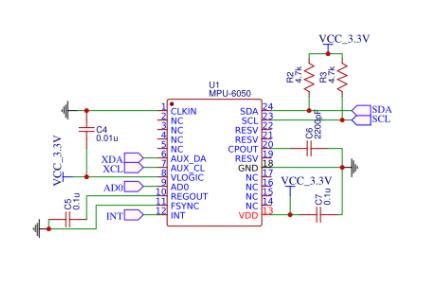
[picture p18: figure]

Figure15 : MPU 6050 breakout schematic

Feature | Value
Gyro fullscale [dps] | ±250 ±500 ±1000 ±2000
Gyro sensitivity [LSB/dps] | 131 65.5 32.8 16.4
Gyro output data rate | 8KHz max
Accelerometer fullscale [g] | ±2 ±4 ±8 ±16
Accelerometer sensitivity [LSB/g] | 16 ,384 8192 4096 2048
Accelerometer output data rate | 1KHz max
Digital Output | I²C
Shock resistant | 10,000g
Power consumption | I = 3.8mA, V =2.375v-3.46v

את החיישן יש להגדיר )config )לאחר עליית המתח לרכיב. יש להגדיר רזולוציה )scale full )עבור gyro ועבור הaccelerometer, כמו כן יש להגדיר את קצב רענון הנתונים – הrate data output. לאחר מכן, ניתן לקרוא באופן יזום בכל רגע נתון את דגימות החיישן, ולאחסן אותן בבקר לצורך שליחה.

## 5 ארכיטקטורת תוכנה

### 5.1 ארכיטקטורה

### 5.1.1 מבנה שכבות הקוד

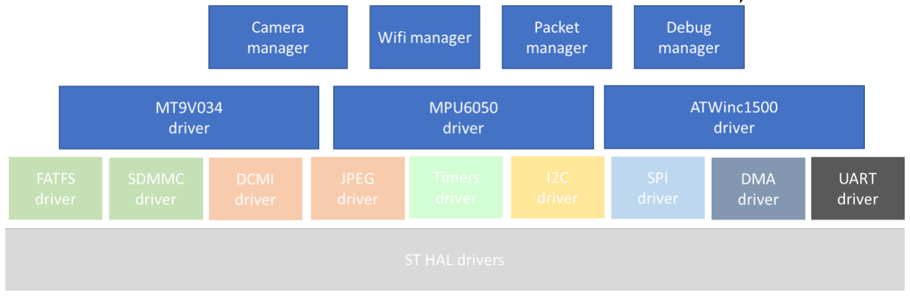
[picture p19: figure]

### 5.1.1.1 שלב האתחול של הבקר

עליית הקוד צריכה להבטיח הדלקת הפריפריות, הקצאת הזכרונות, הגדרות השעונים ואתחול כל מודול חומרתי לפי הפרמטרים שפורטו בפרק הקודם. הקוד מתחיל מהגדרת מרחבי הזכרון בתחילת ריצת הקוד, לאחר מכן אתחול הHAL ( Layer Abstraction Hardware -שכבת קוד שחברת STMicro מפרסמת כהפשטה של שכבת החומרה בבקר, לדרייברים תכנתיים פשוטים יותר(, הגדרות שעונים, ולאחר מכן אתחול של כל שאר הפריפריות והמודולים שלנו לפי השעונים והזכרונות שהוקצו להם .

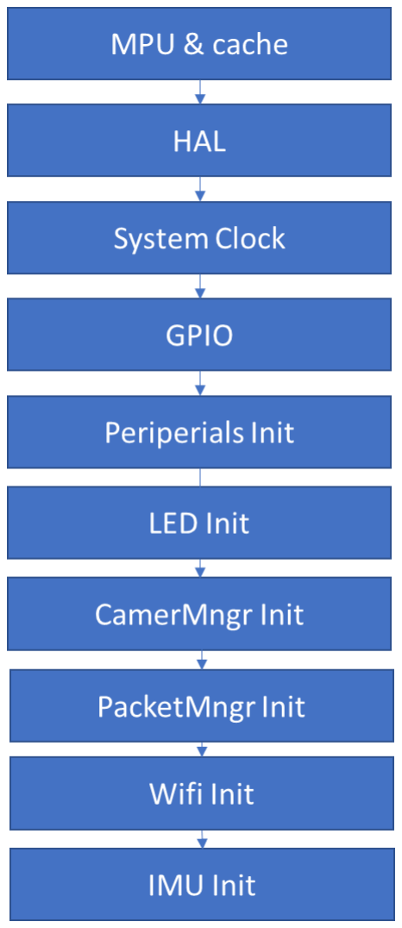
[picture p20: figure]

### 5.1.1.2 לוגיקת תפיסת התמונה ודחיסתה

להלן מצורף תרשים הזמן על תפיסת התמונה, דחיסתה והכנתה לשליחה, בכל פרק זמן של אירוע שליחה שמוגדר אחת ל msec60 כפי ששותפי לעבודה על המוצר הגדיר בקובץ h.mng_packet.

Figure 16 : compression timeline

Figure 17 : Image handling routine

מובא כאן פלט debug בזמן אמת של תקשורת מול תחנת קרקע. זהו צילום מסך של תכנת Docklight שמנגישה את תקשורת ה UART של הבקר.
ליד כל שורה יש חותמת זמן ב msec מרגע עליית הבקר,ובטקסט את האירועים שקורים.

ניתן לראות שהזמן האופייני לתפיסת התמונה ודחיסתה תלוי במאפייני התמונה וכמה היא עשירה בגרדיאנטים זמן אופייני לתפיסת תמונה – עד כ msec.20 זמן אופייני לדחיסת תמונה – כ msec.21

Parameter | Value
SOF | A message with IMAGE data is being sent to ground station
acq s | Acquisition of new frame from camera started
imu | A message with IMU data is being sent to ground station
acq dur X[msec] | Acqusition of frame took X msec
comp s | JPEG compression started
jout size = X[b], jcmp Y[msec] | JPEG compression took Y msec with output of size X bytes

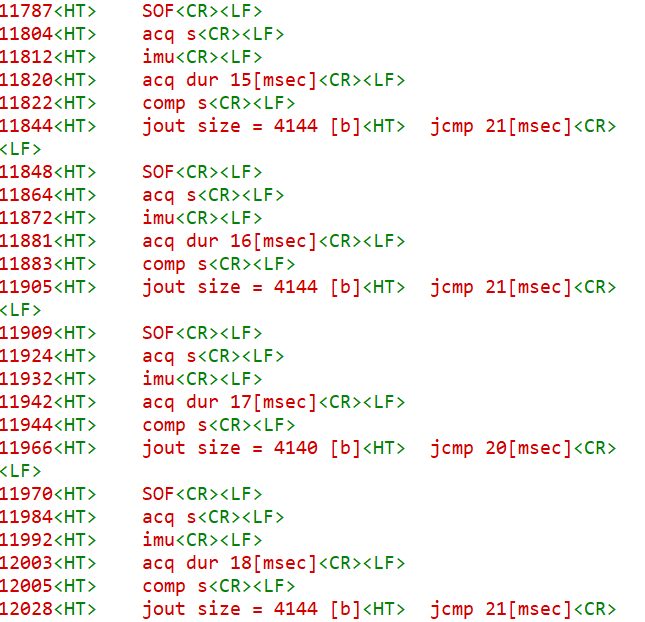
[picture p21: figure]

Figure18 : acquisition and compression debug output

### 5.2 תכנת תחנה קרקעית

לטובת חקר ביצועים ונוחות הפיתוח, פותח כלי להצגת התמונות בזמן אמת כתוספת לתכנת התחנה הקרקאית שפיתח שותפי לפרויקט.

התצוגה מאפשרת לקבל את התמונה העדכנית ומציגה את ההשהיות בקבלת התמונת.

התכנה, בסביבת פייתון מהווה את הניהול והטריגר לתחילת שליחת המידע מהמטע"ד והעברת המידע למחשב.

לציין שבגלל סיבה שאינה ידועה, החלק העליון והתחתון של התמונה יוצא מעוות, לכן בתקנת הקרקע אנו חותכים חלק מהצד העליון והתחתון של התמונה על מנת להביא פריים תקין לתצוגה.

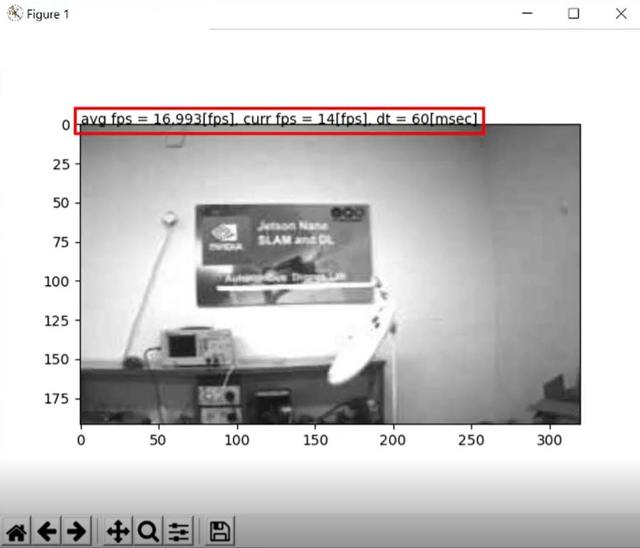
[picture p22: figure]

Figure19 : benchmark and payload's live view

### 5.3 ממשקי DEBUG, צריבה ושימוש במערכת

לצורך פיתוח הקוד והאלגוריתם ולהשמשת המערכת השתמשנו בכלים הבאים:

- הזנת מתח, אפשרית באחת מ2 השיטות הבאות:
- מתח USB באמצעות מחבר USB-micro על הכרטיס )השיטה המומלצת(
- מתח v3.7 מסוללת -LiPo באמצעות מחבר ייעודי ע"ג הכרטיס.
.STM32 | לבקרי | eclipse | מבוסס | debugger -ו compiler - STM32Cube IDE •
- 3V STLINK – צורב לבקר 32STM, מאפשר צריבה דרך JTAG או SWD. בפרויקט הזה השתמשנו בצריבה באמצעות SWD, שאפשר צריבה ע"ג 2 רגליים )SWCLK ,SWDIO), ב header ייעודי ע"ג הOpenMV. הממשק לצורב מצריך גם מתן קו לוגי גבוה V,3.3 קו אדמה משותף GND, ואצלנו מושמש גם קו RESET חיצוני.
- ממיר תקשורת UART to USB – לצורך הצגת הודעות מצב מהמערכת. החיבור מורכב מקו אדמה משותף GND, רגל Tx מהבקר, ורגל Rx מהבקר )לא מושמש תכנתית ממשק Rx).

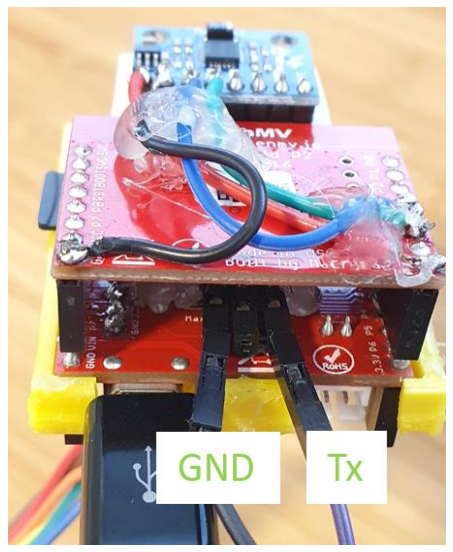
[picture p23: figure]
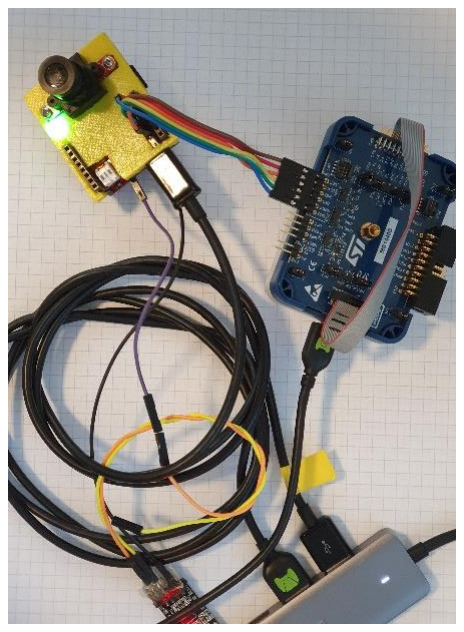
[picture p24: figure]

Figure 20: Debug Setup Figure 21 : UART setup wiring

## 6 תוצאות

### 6.1 תצורת המדידה

בוצעו מדידות להבנת מעטפת הביצועים של המוצר. מערך המדידה כלל חיבור של מצלמת המט"ד לתחנה קרקעית, הקרנת שעון ע"ג התחנה הקרקעית, ושידורה במסך סמוך. הסטאפ הזה הוקלט. לאחר מכן יש תהליך של מיצוי המידע, שהוא מעבר frame-by-frame על הסרטון המוקלט באמצעות תכנה דוגמת player VLC, תיעוד השעון של התחנה הקרקעית )הtruth ground שלנו(, ותיעוד תמונה שהמטע"ד שלח. באמצעות כך יש לנו וקטור של frames עוקבים של המטע"ד והשיהויים בין כל פריים.

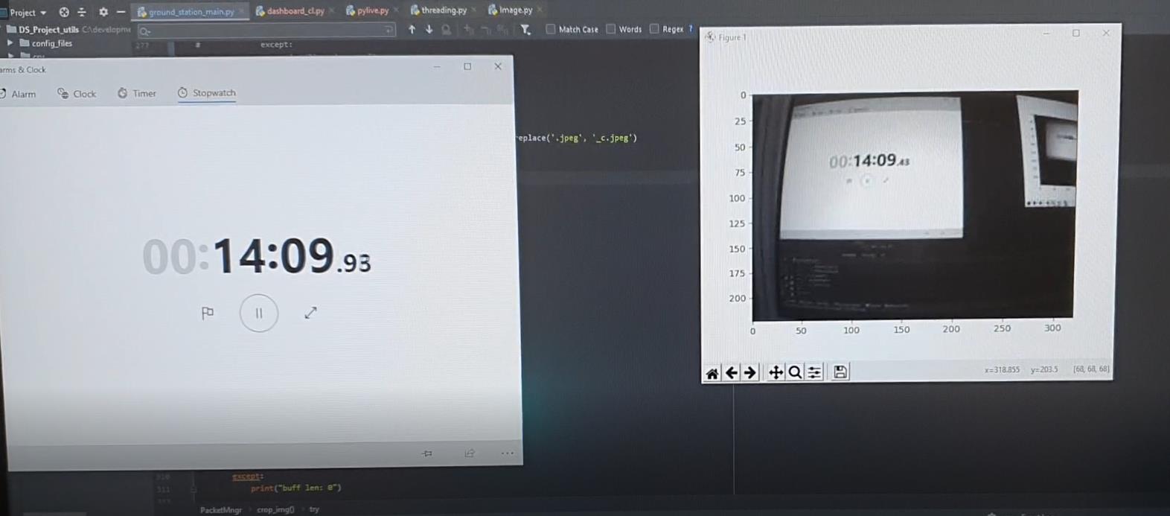
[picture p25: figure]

Figure22 : Delay inspection measuring setup

### 6.2 תוצאות

delay
frames counted | mean delay [msec] | stdev [msec] | max [msec] | min [msec]
16 | 237.50 | 27.73 | 270 | 200

ניתן לראות את ביצועי המערכת, עם שיהוי אופייני של כ msec316 בין כל פריים, עם קצב אופייני של fps16

## 7 סיכום

### 7.1 סיכום

הפרויקט מציג מטע"ד קטן וחדשני, ככלי עזר למחקר ולעבוד המשך, שמביא נתונים ויזואליים-אינרציאליים לתחנת קרקע.

במעבדת הרחפנים האוטונומיים באוניברסיטת תל אביב, נעשה שימוש רב בניווט רחפנים באמצעות SLAM ע"י קבלת מידע חזותי של מיקום הרחפן. ההבנה שהיתוך מידע אינרציאלי יכול לשפר את ביצועי הSLAM, הביאו אותנו לחפש מוצרים שיכולים לתת מענה לבעיה הטכנולוגית.

הפרויקט יצא לדרך מתוך הבנה שלא קיימת מערכת מדף כזו מוכנה לצרכי המעבדה, ועלינו לתכנן ולבנות כזו בעצמנו.

המעבדה סיפקה לנו את הצרכים ההנדסיים שנזדקקנו להם, החל מחומרות, כלי עבודה, סביבת עבודה והנחיה טכנולוגית.

שלבי הפיתוח, מתוך עבודה בסביבת אילוצים נתונה, הביאו אותנו לבצע שיקולים הנדסיים כדוגמת שימוש נבון ברוחב הפס הנתון, עבודה בגודל תמונות וקצב נתונים מסוים.

הפרויקט המשותף של תחנת הקרקע והמטע"ד, שמורים ב repository של מעבדת הרחפנים:

https://github.com/tau-adl/Drones-Navigation-Payload

ברצוני להודות למר יוני מנדל - המנחה שלי בפרויקט הזה, ולשנהב עובדיה- השותף לבניית המערכת הזו.

### 7.2 עבודות המשך

הפרויקט הוכיח היתכנות מבחינת חומרה ותכנה להשלמת מטרת הפרויקט. אולם יש עוד מקום לשיפור - על מנת לתת ביצועים מספקים ואמינים לטובת השמשת אלגוריתמי ניווט ועיבוד processing post ערכי על תחנה קרקעית

.1 השמשת מצבי שינה בבקר, או מציאת תדר עבודה אופטימלי על מנת להשיג צריכות זרמים אופטימליים למטע"ד שמוזן ממתח סוללה

.2 עריכת הרכיבים ע"ג מעגל ייעודי – דבר שיפתור בעיות אלמ"ג, רובוסטיות של המערכת, יקטין גודל ויפחית משקל

.3 בחינת שימוש במצלמה FLIR על מנת לתמוך באפליקציות ניווט לא בחדר סגור

.4 התאמת קצב דגימת המצלמה להתמודדות עם תופעות ריצוד תאורת פלורוסנט בתמונות

.5 בחינת התועלת בתוספת תאורה חיצונית לתמונה – דוגמאת מבזק או תאורה להצפת הסצינה

.6 עבודה עם מודם המטע"ד בתור Client ולא בתור AP, יאפשר עבודה עם תחנה קרקעית אחת אל מול יותר ממטע"ד יחיד

## 8 נספחים

### 8.1 תמונת נוספות של המערכת

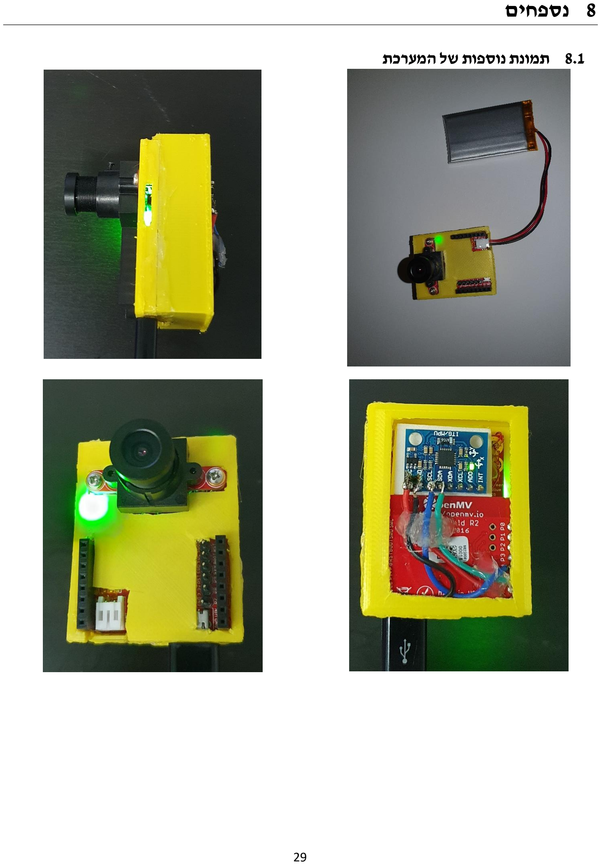
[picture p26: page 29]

### 8.2 ביבליוגרפיה

1. VersaVIS: An Open Versatile Multi-Camera Visual-Inertial Sensor Suite, Florian Tschopp , Mi-chael Riner , Marius Fehr , Lukas Bernreiter , Fadri Furrer , Tonci Novkovic , Andreas Pfrunder , Cesar Cadena , Roland Siegwart , and Juan Nieto, Sensors 2020
2. OpenMv - https://openmv.io/
3. Global Shutter vs. Rolling Shutter image (Figure 1) - https://andor.oxinst.com/learning/view/arti-cle/rolling-and-global-shutter (https://andor.oxinst.com/learning/view/article/rolling-and-global-shutter)
4. Digital Camera Interface – and STmicro document - dm00373474
5. MPU6050 breakout schematic - https://easyeda.com/replicagames/mpu6050
6. MPU6050 driver - https://github.com/sinadarvi/SD_HAL_MPU6050
7. OpenMV repository - https://github.com/openmv/openmv
8. Digital Camera Interface (DCMI) for STM32 MCUs – AN5020
9. On Semiconductor MT9V034 - Datasheet
10. STM32H743xI/G – Datasheet
11. Invensense MPU6050 - Datasheet
12. Microchip ATWINC1500 - Datasheet

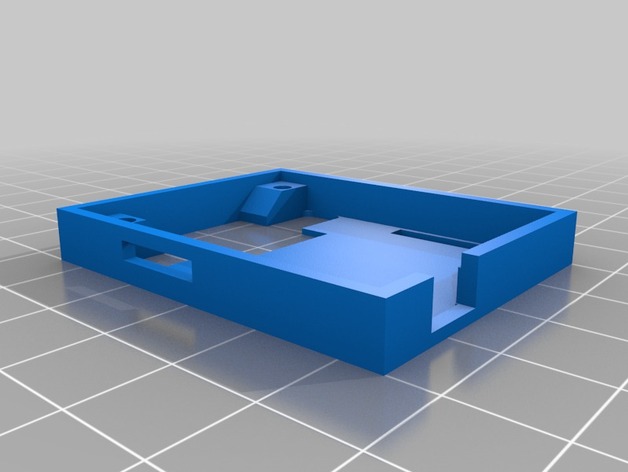
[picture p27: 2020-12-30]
cad/OpenMV_Camera_Case/images/55e02519a19d4640a48d1612c36272f2_preview_featured.jpg

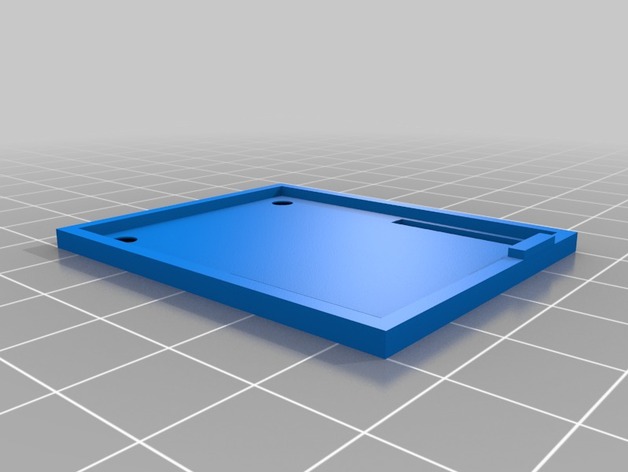
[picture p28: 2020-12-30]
cad/OpenMV_Camera_Case/images/3011db0778eb6c3c6bf6aec033508a93_preview_featured.jpg

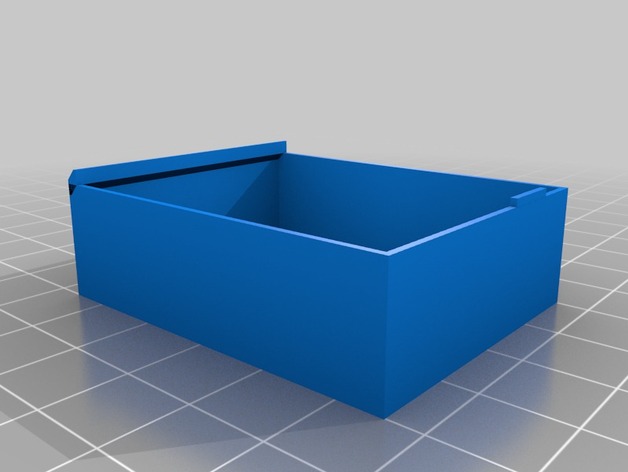
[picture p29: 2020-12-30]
cad/OpenMV_Camera_Case/images/4c3877a2393810d2d2352fbcf820f9d1_preview_featured.jpg

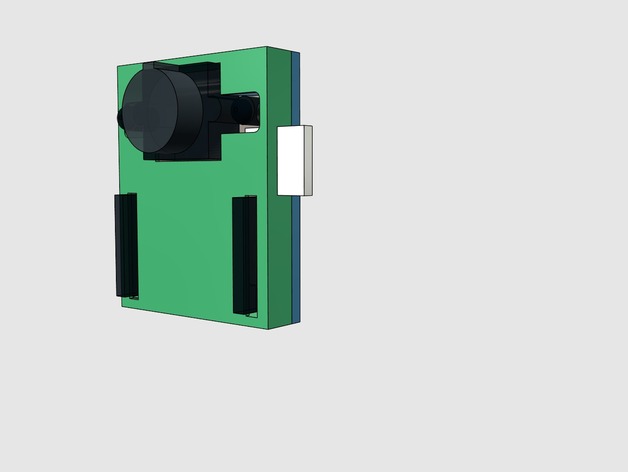
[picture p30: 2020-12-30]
cad/OpenMV_Camera_Case/images/6a401683bb5ca68b7eb194f3d8c03b13_preview_featured.jpg

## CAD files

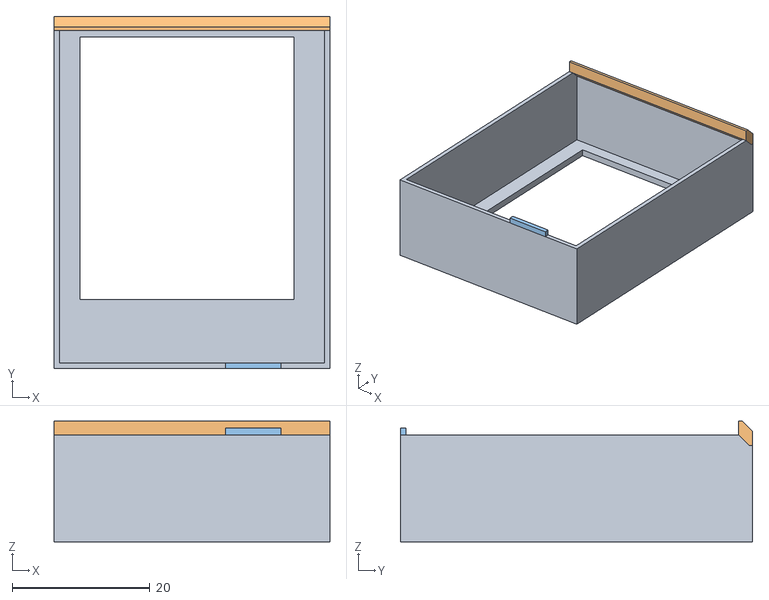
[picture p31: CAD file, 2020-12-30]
cad/OpenMV_Camera_Case/files/OpenMV_rev_7_LCD_cover.stl
40.0 x 51.0 x 17.5

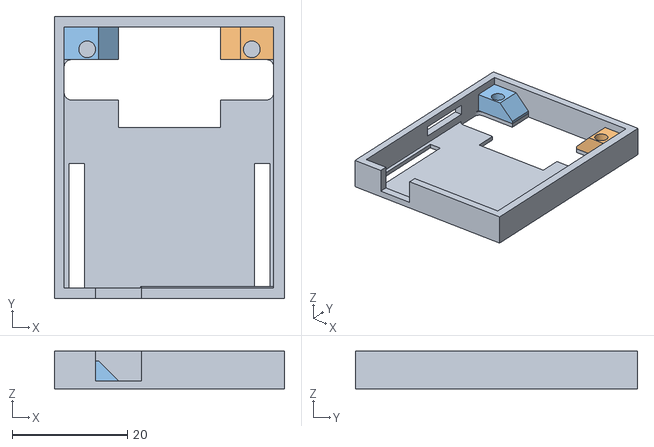
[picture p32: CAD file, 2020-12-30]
cad/OpenMV_Camera_Case/files/OpenMV_rev_6_Camera_Top_cover.stl
40.0 x 49.0 x 6.60

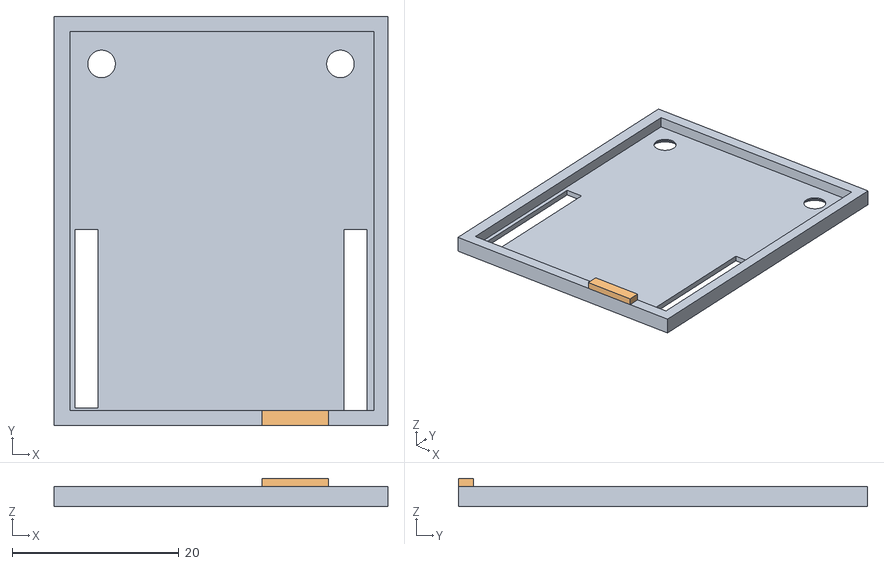
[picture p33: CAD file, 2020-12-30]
cad/OpenMV_Camera_Case/files/OpenMV_rev_6_Camera_Bottom_cover.stl
40.0 x 49.0 x 3.40

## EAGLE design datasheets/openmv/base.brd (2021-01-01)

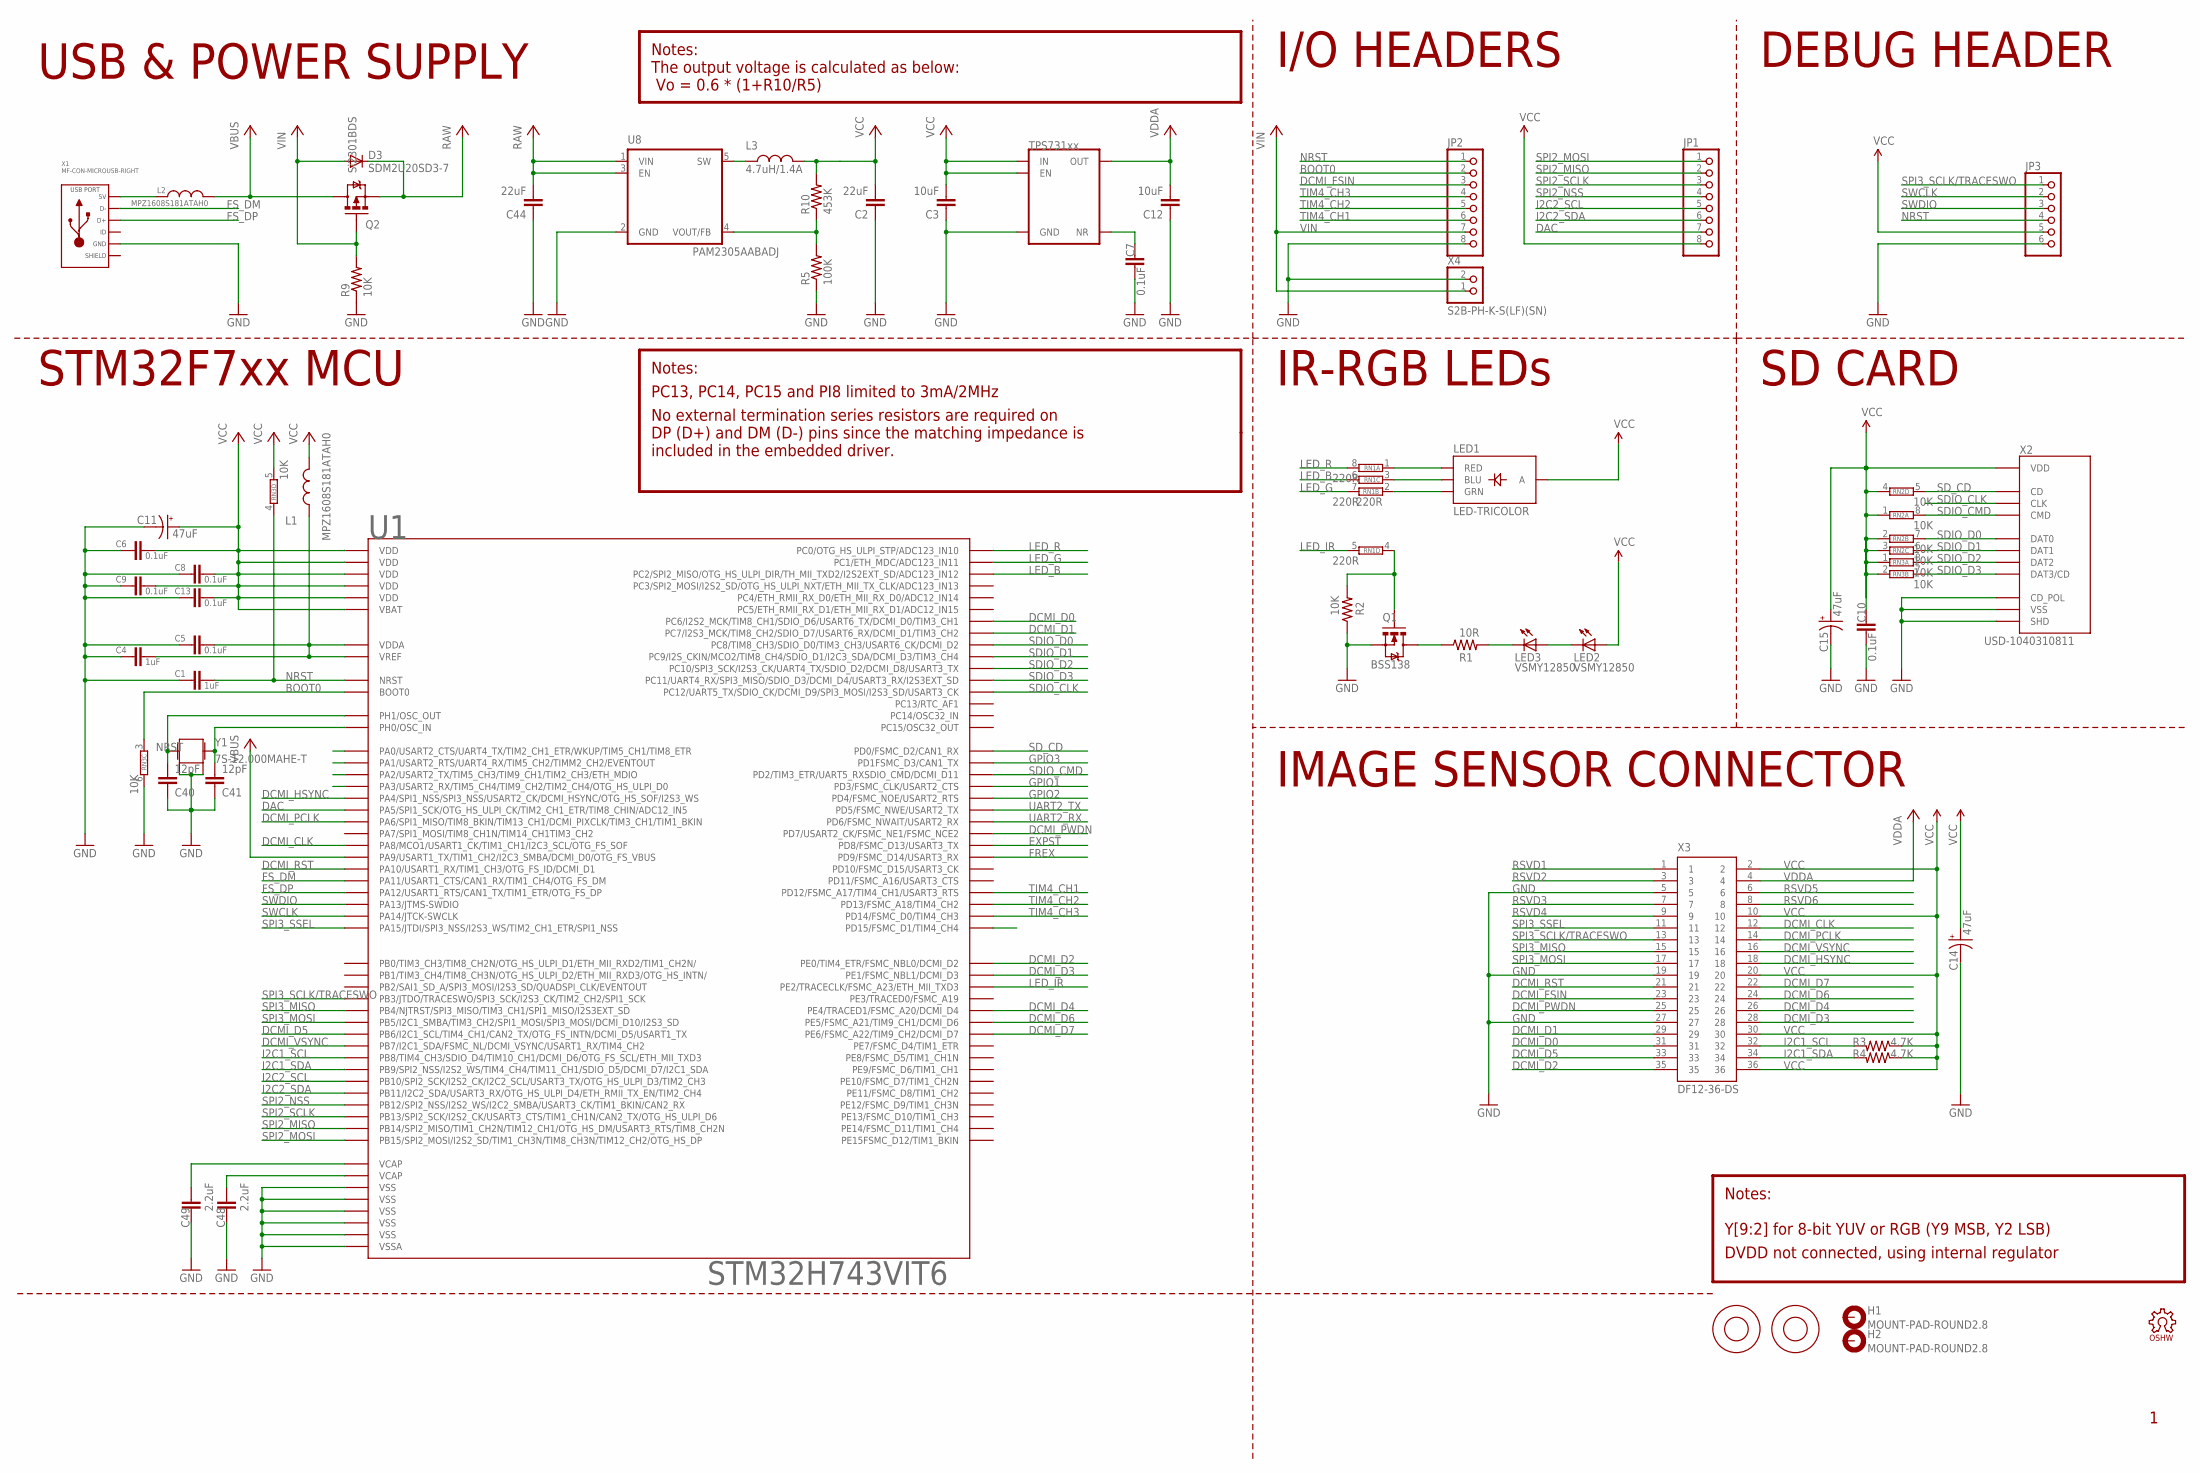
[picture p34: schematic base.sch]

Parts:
C1, C4: 1uF; 0603-CAP
C2, C44: 22uF; 0805
C3, C12: 10uF; 0805
C5, C6, C7, C8, C9, C10, C13: 0.1uF; 0603-CAP
C11, C14, C15: 47uF; EIA3216
C40, C41: 12pF; 0603-CAP
C48, C49: 2.2uF; 0603-CAP
D3: SDM2U20SD3-7; SOD-323
H1, H2: MOUNT-PAD-ROUND2.8; 2,8-PAD
JP1, JP2: PINHD-1X8; 1X08
JP3: PINHD-1X6; 1X06
L1, L2: MPZ1608S181ATAH0; 0603
L3: 4.7uH/1.4A; 1007
LED1: LED-TRICOLOR; LED-TRICOLOR-SMD-MF
LED2, LED3: VSMY12850; LED-1206
LOGO1: OSHW_LOGO_FILLX0100-NT; OSHW_FILLX100_NOTEXT
M1, M2: 9774030243R; 9774030151R
Q1: BSS138; SOT23-3
Q2: Si2301BDS; SOT23-3
R1: 10R; 0603-RES
R2, R9: 10K; 0603-RES
R3, R4: 4.7K; 0603-RES
R5: 100K; 0603-RES
R10: 453K; 0603-RES
RN1: 220R; EXBV8V
RN2, RN3: 10K; EXBV8V
U1: STM32H743VIT6; LQFP100
U5: TPS731XX; SOT23-5
U8: PAM2305AABADJ; TSOT25
X1: MF-CON-MICROUSB-RIGHT; MICROUSB-RIGHT
X2: USD-1040310811; 1040310811
X3: DF12-36-DS
X4: S2B-PH-K-S(LF)(SN); JST-PH-2-THM-RA
Y1: 7S-12.000MAHE-T; CRYSTAL-2.5X2.0

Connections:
BOOT0: JP2.2, RN3.3 (1), U1.94 (BOOT0)
DAC: JP1.7, U1.29 (PA5/SPI1_SCK/OTG_HS_ULPI_CK/TIM2_CH1_ET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)
DCMI_CLK: U1.67 (PA8/MCO1/USART1_CK/TIM1_CH1/I2C3_SCL/OT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), X3.12
DCMI_D0: U1.63 (PC6/I2S2_MCK/TIM8_CH1/SDIO_D6/USART6_TX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), X3.31
DCMI_D1: U1.64 (PC7/I2S3_MCK/TIM8_CH2/SDIO_D7/USART6_RX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), X3.29
DCMI_D2: U1.97 (PE0/TIM4_ETR/FSMC_NBL0/DCMI_D2), X3.35
DCMI_D3: U1.98 (PE1/FSMC_NBL1/DCMI_D3), X3.28
DCMI_D4: U1.3 (PE4/TRACED1/FSMC_A20/DCMI_D4), X3.26
DCMI_D5: U1.92 (PB6/I2C1_SCL/TIM4_CH1/CAN2_TX/OTG_FS_IN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), X3.33
DCMI_D6: U1.4 (PE5/FSMC_A21/TIM9_CH1/DCMI_D6), X3.24
DCMI_D7: U1.5 (PE6/FSMC_A22/TIM9_CH2/DCMI_D7), X3.22
DCMI_FSIN: JP2.3, X3.23
DCMI_HSYNC: U1.28 (PA4/SPI1_NSS/SPI3_NSS/USART2_CK/DCMI_HS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), X3.18
DCMI_PCLK: U1.30 (PA6/SPI1_MISO/TIM8_BKIN/TIM13_CH1/DCMI_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), X3.14
DCMI_PWDN: U1.88 (PD7/USART2_CK/FSMC_NE1/FSMC_NCE2), X3.25
DCMI_RST: U1.69 (PA10/USART1_RX/TIM1_CH3/OTG_FS_ID/DCMI_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), X3.21
DCMI_VSYNC: U1.93 (PB7/I2C1_SDA/FSMC_NL/DCMI_VSYNC/USART1_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), X3.16
EXPST: U1.55 (PD8/FSMC_D13/USART3_TX)
FREX: U1.56 (PD9/FSMC_D14/USART3_RX)
FS_DM: U1.70 (PA11/USART1_CTS/CAN1_RX/TIM1_CH4/OTG_FS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), X1.2 (D-)
FS_DP: U1.71 (PA12/USART1_RTS/CAN1_TX/TIM1_ETR/OTG_FS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), X1.3 (D+)
GND: C1.2, C2.1, C3.1, C4.2, C5.2, C6.2, C7.2, C8.2, C9.2, C10.2, C11.C (-), C12.1, C13.2, C14.C (-), C15.C (-), C40.1, C41.1, C44.1, C48.2, C49.2, JP2.8, JP3.6, Q1.2 (S), R2.1, R5.1, R9.1, RN3.6 (2), U1.10 (VSS), U1.19 (VSSA), U1.26 (VSS), U1.49 (VSS), U1.74 (VSS), U1.99 (VSS), U5.2 (GND), U8.2 (GND), X1.5 (GND), X2.CD$2 (CD_POL), X2.G$1 (SHD), X2.G$2 (SHD), X2.G$3 (SHD), X2.G$4 (SHD), X2.P$6 (VSS), X3.5, X3.19, X3.27, X4.2 (1), Y1.2, Y1.4
GPIO1: U1.84 (PD3/FSMC_CLK/USART2_CTS)
GPIO2: U1.85 (PD4/FSMC_NOE/USART2_RTS)
GPIO3: U1.82 (PD1FSMC_D3/CAN1_TX)
I2C1_SCL: R3.2, U1.95 (PB8/TIM4_CH3/SDIO_D4/TIM10_CH1/DCMI_D6/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), X3.32
I2C1_SDA: R4.2, U1.96 (PB9/SPI2_NSS/I2S2_WS/TIM4_CH4/TIM11_CH1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), X3.34
I2C2_SCL: JP1.5, U1.46 (PB10/SPI2_SCK/I2S2_CK/I2C2_SCL/USART3_T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)
I2C2_SDA: JP1.6, U1.47 (PB11/I2C2_SDA/USART3_RX/OTG_HS_ULPI_D4/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)
LED_B: RN1.6 (2), U1.17 (PC2/SPI2_MISO/OTG_HS_ULPI_DIR/TH_MII_TX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)
LED_G: RN1.7 (2), U1.16 (PC1/ETH_MDC/ADC123_IN11)
LED_IR: RN1.5 (2), U1.1 (PE2/TRACECLK/FSMC_A23/ETH_MII_TXD3)
LED_R: RN1.8 (2), U1.15 (PC0/OTG_HS_ULPI_STP/ADC123_IN10)
unnamed: C40.2, U1.13 (PH1/OSC_OUT), Y1.3 (2)
unnamed: C41.2, U1.12 (PH0/OSC_IN), Y1.1
unnamed: Q1.1 (G), R2.2, RN1.4 (1)
unnamed: LED1.B (BLU), RN1.3 (1)
unnamed: L2.1, X1.1 (5V)
unnamed: LED1.R (RED), RN1.1
unnamed: LED1.G (GRN), RN1.2 (1)
unnamed: LED3.C, R1.2
unnamed: C7.1, U5.4 (NR)
unnamed: C4.1, C5.1, L1.1, U1.20 (VREF), U1.21 (VDDA)
unnamed: R5.2, R10.1, U8.4 (VOUT/FB)
unnamed: Q1.3 (D), R1.1
unnamed: LED2.C, LED3.A
NRST: C1.1, JP2.1, JP3.4, RN3.4 (1), U1.14 (NRST)
RAW: C44.2, D3.1 (C), Q2.2 (S), U8.1 (VIN), U8.3 (EN)
RSVD1: X3.1
RSVD2: X3.3
RSVD3: X3.7
RSVD4: X3.9
RSVD5: X3.6
RSVD6: X3.8
SDIO_CLK: U1.80 (PC12/UART5_TX/SDIO_CK/DCMI_D9/SPI3_MOSI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), X2.P$5 (CLK)
SDIO_CMD: RN2.8 (2), U1.83 (PD2/TIM3_ETR/UART5_RXSDIO_CMD/DCMI_D11), X2.P$3 (CMD)
SDIO_D0: RN2.7 (2), U1.65 (PC8/TIM8_CH3/SDIO_D0/TIM3_CH3/USART6_CK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), X2.P$7 (DAT0)
SDIO_D1: RN2.6 (2), U1.66 (PC9/I2S_CKIN/MCO2/TIM8_CH4/SDIO_D1/I2C3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), X2.P$8 (DAT1)
SDIO_D2: RN3.8 (2), U1.78 (PC10/SPI3_SCK/I2S3_CK/UART4_TX/SDIO_D2/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), X2.P$1 (DAT2)
SDIO_D3: RN3.7 (2), U1.79 (PC11/UART4_RX/SPI3_MISO/SDIO_D3/DCMI_D4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), X2.P$2 (DAT3/CD)
SD_CD: RN2.5 (2), U1.81 (PD0/FSMC_D2/CAN1_RX), X2.CD$1 (CD)
SPI2_MISO: JP1.2, U1.53 (PB14/SPI2_MISO/TIM1_CH2N/TIM12_CH1/OTG_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)
SPI2_MOSI: JP1.1, U1.54 (PB15/SPI2_MOSI/I2S2_SD/TIM1_CH3N/TIM8_C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)
SPI2_NSS: JP1.4, U1.51 (PB12/SPI2_NSS/I2S2_WS/I2C2_SMBA/USART3_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)
SPI2_SCLK: JP1.3, U1.52 (PB13/SPI2_SCK/I2S2_CK/USART3_CTS/TIM1_C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)
SPI3_MISO: U1.90 (PB4/NJTRST/SPI3_MISO/TIM3_CH1/SPI1_MISO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), X3.15
SPI3_MOSI: U1.91 (PB5/I2C1_SMBA/TIM3_CH2/SPI1_MOSI/SPI3_M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), X3.17
SPI3_SCLK/TRACESWO: JP3.1, U1.89 (PB3/JTDO/TRACESWO/SPI3_SCK/I2S3_CK/TIM2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), X3.13
SPI3_SSEL: U1.77 (PA15/JTDI/SPI3_NSS/I2S3_WS/TIM2_CH1_ETR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), X3.11
SW: L3.1, U8.5 (SW)
SWCLK: JP3.2, U1.76 (PA14/JTCK-SWCLK)
SWDIO: JP3.3, U1.72 (PA13/JTMS-SWDIO)
TIM4_CH1: JP2.6, U1.59 (PD12/FSMC_A17/TIM4_CH1/USART3_RTS)
TIM4_CH2: JP2.5, U1.60 (PD13/FSMC_A18/TIM4_CH2)
TIM4_CH3: JP2.4, U1.61 (PD14/FSMC_D0/TIM4_CH3)
UART2_RX: U1.87 (PD6/FSMC_NWAIT/USART2_RX)
UART2_TX: U1.86 (PD5/FSMC_NWE/USART2_TX)
VBUS: L2.2, Q2.3 (D), U1.68 (PA9/USART1_TX/TIM1_CH2/I2C3_SMBA/DCMI_D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)
VCAP1: C49.1, U1.48 (VCAP)
VCAP2: C48.1, U1.73 (VCAP)
VCC: C2.2, C3.2, C6.1, C8.1, C9.1, C10.1, C11.A (+), C13.1, C14.A (+), C15.A (+), JP1.8, JP3.5, L1.2, L3.2, LED1.A, LED2.A, R3.1, R4.1, R10.2, RN2.1, RN2.2 (1), RN2.3 (1), RN2.4 (1), RN3.1, RN3.2 (1), RN3.5 (2), U1.6 (VBAT), U1.11 (VDD), U1.27 (VDD), U1.50 (VDD), U1.75 (VDD), U1.100 (VDD), U5.1 (IN), U5.3 (EN), X2.P$4 (VDD), X3.2, X3.10, X3.20, X3.30, X3.36
VDDA: C12.2, U5.5 (OUT), X3.4
VIN: D3.2 (A), JP2.7, Q2.1 (G), R9.2, X4.1 (2)

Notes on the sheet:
PC13, PC14, PC15 and PI8 limited to 3mA/2MHz
SD CARD
Y[9:2] for 8-bit YUV or RGB (Y9 MSB, Y2 LSB)
DVDD not connected, using internal regulator
Notes:
IMAGE SENSOR CONNECTOR
STM32F7xx MCU
IR-RGB LEDs
USB & POWER SUPPLY
DEBUG HEADER
I/O HEADERS
No external termination series resistors are required on DP (D+) and DM (D-) pins since the matching impedance is included in the embedded driver.
The output voltage is calculated as below: Vo = 0.6 * (1+R10/R5)

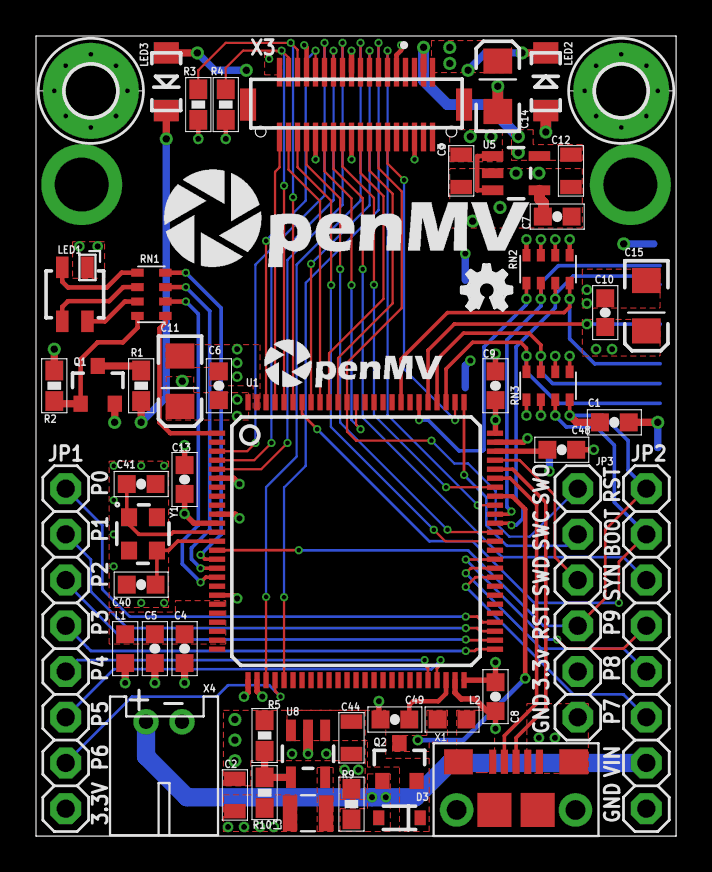
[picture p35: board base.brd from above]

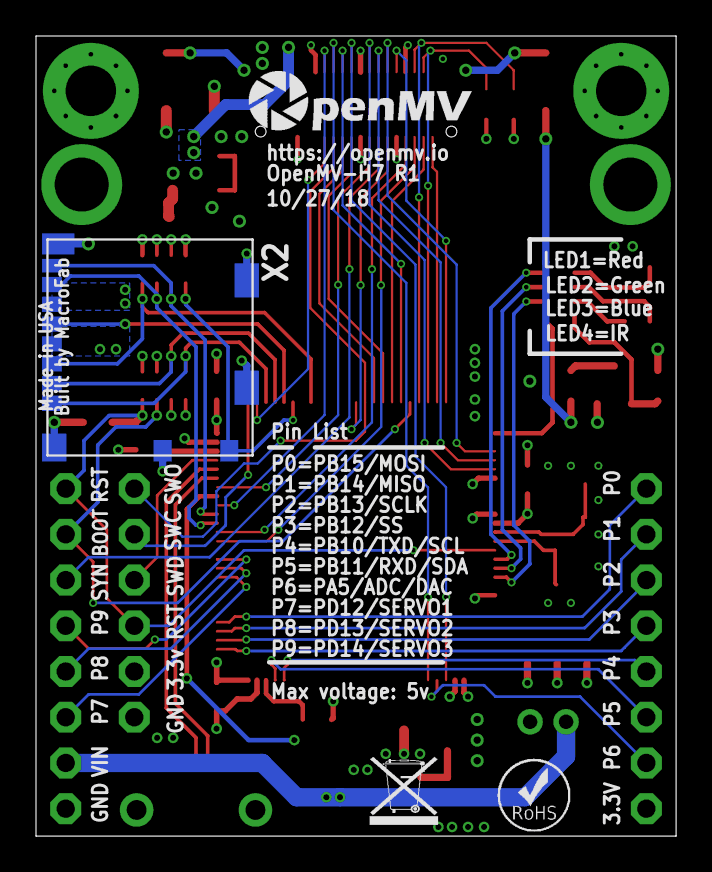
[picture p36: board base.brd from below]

Board: 4 copper layers, 35.6 x 44.5 mm, 60 parts (4 on the bottom side), 70 nets.

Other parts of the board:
U$1: WEEE
U$2: ROHS
U$3: OMV-LOGO
U$4: OMV-LOGO-SMALL
U$6: OMV-LOGO-BIG

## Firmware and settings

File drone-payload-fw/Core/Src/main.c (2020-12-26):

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
/* Includes ------------------------------------------------------------------*/
#include "main.h"
#include "dcmi.h"
#include "dma.h"
#include "fatfs.h"
#include "i2c.h"
#include "jpeg.h"
#include "mdma.h"
#include "sdmmc.h"
#include "spi.h"
#include "tim.h"
#include "usart.h"
#include "gpio.h"

/* USER CODE BEGIN Includes */
#include <stdbool.h>
#include "debug_mngr.h"
#include "config/conf_winc.h"
#include "driver/include/m2m_types.h"
#include "wifi_mngr.h"
#include "led.h"

#include "jpeg_utils_conf.h"
#include "jpeg_utils.h"
#include "jpeg_encode_dma.h"
#include "f_op_playground.h"

#include "sd_hal_mpu6050.h"
#include "packet_mngr.h"
#include "camera_mngr.h"
#include "sensor.h"
/* USER CODE END Includes */


void SystemClock_Config(void);
static void MPU_Config(void);
/**
  * @brief  The application entry point.
  * @retval int
  */
int main(void)
{
  /* USER CODE BEGIN 1 */
	uint32_t ImuInitRes = SD_MPU6050_Result_Error;
	int8_t WifiInitRes = M2M_ERR_INIT;
  /* USER CODE END 1 */

  /* MPU Configuration--------------------------------------------------------*/
  MPU_Config();

  /* Enable I-Cache---------------------------------------------------------*/
  SCB_EnableICache();

  /* Enable D-Cache---------------------------------------------------------*/
  SCB_EnableDCache();

  /* MCU Configuration--------------------------------------------------------*/

  /* Reset of all peripherals, Initializes the Flash interface and the Systick. */
  HAL_Init();

  /* Configure the system clock */
  SystemClock_Config();

  /* Initialize all configured peripherals */
  MX_GPIO_Init();
  MX_MDMA_Init();
  MX_JPEG_Init();
  MX_DMA_Init();
  MX_I2C1_Init();
  MX_DCMI_Init();
  MX_SDMMC1_SD_Init();
  MX_FATFS_Init();
  MX_TIM2_Init();
  MX_I2C2_Init();
  MX_UART4_Init();
  MX_TIM1_Init();
  MX_TIM6_Init();
  /* USER CODE BEGIN 2 */
	LED_Init();
	CameraMngr_Init();
	PacketMngr_Init();

	WifiInitRes = WifiMngr_Init();

	ImuInitRes = SD_MPU6050_Init(SD_MPU6050_Device_0, SD_MPU6050_Accelerometer_2G, SD_MPU6050_Gyroscope_250s );

	if (WifiInitRes != M2M_SUCCESS)
	{
		printf("wifi init err\r\n");
	}
	else
	{
		printf("wifi init ok\r\n");
	}

	if (ImuInitRes != SD_MPU6050_Result_Ok)
	{
		printf("imu init err\r\n");
	}
	else
	{
		printf("imu init ok\r\n");
	}

	printf("~~ init finished ~~\r\n");
	printf("GIT REV SHA: %s\r\n", PROJ_SHA);

  /* USER CODE END 2 */

  /* Infinite loop */
  /* USER CODE BEGIN WHILE */
	while( true )
	{
		CameraMngr_HandleEvents();

		WifiMngr_HandleEvents();

    /* USER CODE END WHILE */

    /* USER CODE BEGIN 3 */
	}
  /* USER CODE END 3 */
}

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
/* USER CODE BEGIN 4 */

// TODO: DB - define in cube and move to `stm32h7xx_it.h`
void HAL_GPIO_EXTI_Callback(uint16_t GPIO_Pin)
{
	if (GPIO_Pin == CONF_WINC_SPI_INT_PIN)
	{
		isr();
	}
}

/* USER CODE END 4 */

/* MPU Configuration */

void MPU_Config(void)
{
  MPU_Region_InitTypeDef MPU_InitStruct = {0};

  /* Disables the MPU */
  HAL_MPU_Disable();
  /** Initializes and configures the Region and the memory to be protected
  */
  MPU_InitStruct.Enable = MPU_REGION_ENABLE;
  MPU_InitStruct.Number = MPU_REGION_NUMBER0;
  MPU_InitStruct.BaseAddress = 0x24000000;
  MPU_InitStruct.Size = MPU_REGION_SIZE_512KB;
  MPU_InitStruct.SubRegionDisable = 0x0;
  MPU_InitStruct.TypeExtField = MPU_TEX_LEVEL0;
  MPU_InitStruct.AccessPermission = MPU_REGION_FULL_ACCESS;
  MPU_InitStruct.DisableExec = MPU_INSTRUCTION_ACCESS_ENABLE;
  MPU_InitStruct.IsShareable = MPU_ACCESS_NOT_SHAREABLE;
  MPU_InitStruct.IsCacheable = MPU_ACCESS_CACHEABLE;
  MPU_InitStruct.IsBufferable = MPU_ACCESS_NOT_BUFFERABLE;

  HAL_MPU_ConfigRegion(&MPU_InitStruct);
  /* Enables the MPU */
  HAL_MPU_Enable(MPU_PRIVILEGED_DEFAULT);

}

/**
  * @brief  This function is executed in case of error occurrence.
  * @retval None
  */
void Error_Handler(void)
{
  /* USER CODE BEGIN Error_Handler_Debug */
	printf("\r\n***Error_handler***\r\n");
	while (true)
	{
		HAL_Delay(500);
		LED_SetState(eLedStates_red);
		HAL_Delay(500);
		LED_SetState(eLedStates_all_off);
	}
  /* USER CODE END Error_Handler_Debug */
}

#ifdef  USE_FULL_ASSERT
/**
  * @brief  Reports the name of the source file and the source line number
  *         where the assert_param error has occurred.
  * @param  file: pointer to the source file name
  * @param  line: assert_param error line source number
  * @retval None
  */
void assert_failed(uint8_t *file, uint32_t line)
{
  /* USER CODE BEGIN 6 */
	/* User can add his own implementation to report the file name and line number,
	 tex: printf("Wrong parameters value: file %s on line %d\r\n", file, line) */
	printf("\r\n***assert_failed***\r\n");
	printf("Wrong parameters value: file %s on line %d\r\n", file, line);
	while (true)
	{
		HAL_Delay(500);
		LED_SetState(eLedStates_red);
		HAL_Delay(500);
		LED_SetState(eLedStates_all_off);
	}

  /* USER CODE END 6 */
}
#endif /* USE_FULL_ASSERT */

/************************ (C) COPYRIGHT STMicroelectronics *****END OF FILE****/

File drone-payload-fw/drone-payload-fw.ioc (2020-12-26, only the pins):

Mcu.UserName=STM32H743VITx
PA0.Signal=UART4_TX
PA1.Signal=UART4_RX
PA10.GPIO_Label=DCMI_RESET
PA10.Signal=GPIO_Output
PA4.Signal=DCMI_HSYNC
PA5.GPIO_Label=WIFI_CHIP_EN
PA5.Signal=GPIO_Output
PA6.Signal=DCMI_PIXCLK
PA8.GPIO_Label=DCMI_PCLK
PA8.Signal=S_TIM1_CH1
PB10.Signal=I2C2_SCL
PB11.Signal=I2C2_SDA
PB12.GPIO_Label=SPI2_NSS
PB12.Signal=GPIO_Output
PB13.Signal=SPI2_SCK
PB14.Signal=SPI2_MISO
PB15.Signal=SPI2_MOSI
PB6.Signal=DCMI_D5
PB7.Signal=DCMI_VSYNC
PB8.Signal=I2C1_SCL
PB9.Signal=I2C1_SDA
PC0.GPIO_Label=LED_R
PC0.Signal=GPIO_Output
PC1.GPIO_Label=LED_G
PC1.Signal=GPIO_Output
PC12.Signal=SDMMC1_CK
PC2_C.GPIO_Label=LED_B
PC2_C.Signal=GPIO_Output
PC6.Signal=DCMI_D0
PC7.Signal=DCMI_D1
PC8.Signal=SDMMC1_D0
PD0.GPIO_Label=SD_CD
PD0.Signal=GPIO_Input
PD12.GPIO_Label=WIFI_RESET_N
PD12.Signal=GPIO_Output
PD13.GPIO_Label=WIFI_INT_N
PD13.Signal=GPXTI13
PD2.Signal=SDMMC1_CMD
PD7.GPIO_Label=DCMI_PWDN
PD7.Signal=GPIO_Output
PE0.Signal=DCMI_D2
PE1.Signal=DCMI_D3
PE4.Signal=DCMI_D4
PE5.Signal=DCMI_D6
PE6.Signal=DCMI_D7

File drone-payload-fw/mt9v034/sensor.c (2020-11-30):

/*
 * This file is part of the OpenMV project.
 *
 * Copyright (c) 2013-2019 Ibrahim Abdelkader <iabdalkader@openmv.io>
 * Copyright (c) 2013-2019 Kwabena W. Agyeman <kwagyeman@openmv.io>
 *
 * This work is licensed under the MIT license, see the file LICENSE for details.
 *
 * Sensor abstraction layer.
 */
#include <stdlib.h>
#include <string.h>
//#include "mp.h"
//#include "irq.h"
#include "cambus.h"

#include "mt9v034.h"

#include "sensor.h"
//#include "systick.h"
//#include "framebuffer.h"
#include "omv_boardconfig.h"

#define MAX_XFER_SIZE   (0xFFFF*4)

sensor_t           sensor     = {0};
TIM_HandleTypeDef  TIMHandle  = {0};
DMA_HandleTypeDef  DMAHandle  = {0};
DCMI_HandleTypeDef DCMIHandle = {0};

static volatile int line = 0;
extern uint8_t _line_buf;
static uint8_t *dest_fb = NULL;

const int resolution[][2] = {
    {0,    0   },
    // C/SIF Resolutions
    {88,   72  },    /* QQCIF     */
    {176,  144 },    /* QCIF      */
    {352,  288 },    /* CIF       */
    {88,   60  },    /* QQSIF     */
    {176,  120 },    /* QSIF      */
    {352,  240 },    /* SIF       */
    // VGA Resolutions
    {40,   30  },    /* QQQQVGA   */
    {80,   60  },    /* QQQVGA    */
    {160,  120 },    /* QQVGA     */
    {320,  240 },    /* QVGA      */
    {640,  480 },    /* VGA       */
    {60,   40  },    /* HQQQVGA   */
    {120,  80  },    /* HQQVGA    */
    {240,  160 },    /* HQVGA     */
    // FFT Resolutions
    {64,   32  },    /* 64x32     */
    {64,   64  },    /* 64x64     */
    {128,  64  },    /* 128x64    */
    {128,  128 },    /* 128x64    */
    // Other
    {128,  160 },    /* LCD       */
    {128,  160 },    /* QQVGA2    */
    {720,  480 },    /* WVGA      */
    {752,  480 },    /* WVGA2     */
    {800,  600 },    /* SVGA      */
    {1024, 768 },    /* XGA       */
    {1280, 1024},    /* SXGA      */
    {1600, 1200},    /* UXGA      */
    {1280, 720 },    /* HD        */
    {1920, 1080},    /* FHD       */
    {2560, 1440},    /* QHD       */
    {2048, 1536},    /* QXGA      */
    {2560, 1600},    /* WQXGA     */
    {2592, 1944},    /* WQXGA2    */
};

static int extclk_config(int frequency)
{
    #if (OMV_XCLK_SOURCE == OMV_XCLK_TIM)
    /* TCLK (PCLK * 2) */
    int tclk = DCMI_TIM_PCLK_FREQ() * 2;

    /* Period should be even */
    int period = (tclk / frequency) - 1;

    if (TIMHandle.Init.Period && (TIMHandle.Init.Period != period)) {
        // __HAL_TIM_SET_AUTORELOAD sets TIMHandle.Init.Period...
        __HAL_TIM_SET_AUTORELOAD(&TIMHandle, period);
        __HAL_TIM_SET_COMPARE(&TIMHandle, DCMI_TIM_CHANNEL, period / 2);
        return 0;
    }

    /* Timer base configuration */
    TIMHandle.Instance           = DCMI_TIM;
    TIMHandle.Init.Period        = period;
    TIMHandle.Init.Prescaler     = TIM_ETRPRESCALER_DIV1;
    TIMHandle.Init.CounterMode   = TIM_COUNTERMODE_UP;
    TIMHandle.Init.ClockDivision = TIM_CLOCKDIVISION_DIV1;

    /* Timer channel configuration */
    TIM_OC_InitTypeDef TIMOCHandle;
    TIMOCHandle.Pulse       = period / 2;
    TIMOCHandle.OCMode      = TIM_OCMODE_PWM1;
    TIMOCHandle.OCPolarity  = TIM_OCPOLARITY_HIGH;
    TIMOCHandle.OCNPolarity = TIM_OCNPOLARITY_HIGH; // TODO: this was not in the original OMV code
    TIMOCHandle.OCFastMode  = TIM_OCFAST_DISABLE;
    TIMOCHandle.OCIdleState = TIM_OCIDLESTATE_RESET;
    TIMOCHandle.OCNIdleState = TIM_OCNIDLESTATE_RESET;  // TODO: this was not in the original OMV code

    if ((HAL_TIM_PWM_Init(&TIMHandle) != HAL_OK)
    || (HAL_TIM_PWM_ConfigChannel(&TIMHandle, &TIMOCHandle, DCMI_TIM_CHANNEL) != HAL_OK)
    || (HAL_TIM_PWM_Start(&TIMHandle, DCMI_TIM_CHANNEL) != HAL_OK)) {
        return -1;
    }
    #endif // (OMV_XCLK_SOURCE == OMV_XCLK_TIM)

    return 0;
}

static int dcmi_config(uint32_t jpeg_mode)
{
	// TODO: uncommnet
//    // DCMI configuration
//    DCMIHandle.Instance         = DCMI;
//    // VSYNC clock polarity
//    DCMIHandle.Init.VSPolarity  = SENSOR_HW_FLAGS_GET(&sensor, SENSOR_HW_FLAGS_VSYNC) ?
//                                    DCMI_VSPOLARITY_HIGH : DCMI_VSPOLARITY_LOW;
//    // HSYNC clock polarity
//    DCMIHandle.Init.HSPolarity  = SENSOR_HW_FLAGS_GET(&sensor, SENSOR_HW_FLAGS_HSYNC) ?
//                                    DCMI_HSPOLARITY_HIGH : DCMI_HSPOLARITY_LOW;
//    // PXCLK clock polarity
//    DCMIHandle.Init.PCKPolarity = SENSOR_HW_FLAGS_GET(&sensor, SENSOR_HW_FLAGS_PIXCK) ?
//                                    DCMI_PCKPOLARITY_RISING : DCMI_PCKPOLARITY_FALLING;
//
//    DCMIHandle.Init.SynchroMode = DCMI_SYNCHRO_HARDWARE;    // Enable Hardware synchronization
//    DCMIHandle.Init.CaptureRate = DCMI_CR_ALL_FRAME;        // Capture rate all frames
//    DCMIHandle.Init.ExtendedDataMode = DCMI_EXTEND_DATA_8B; // Capture 8 bits on every pixel clock
//    DCMIHandle.Init.JPEGMode = jpeg_mode;                   // Set JPEG Mode
//    #if defined(MCU_SERIES_F7) || defined(MCU_SERIES_H7)
//    DCMIHandle.Init.ByteSelectMode  = DCMI_BSM_ALL;         // Capture all received bytes
//    DCMIHandle.Init.ByteSelectStart = DCMI_OEBS_ODD;        // Ignored
//    DCMIHandle.Init.LineSelectMode  = DCMI_LSM_ALL;         // Capture all received lines
//    DCMIHandle.Init.LineSelectStart = DCMI_OELS_ODD;        // Ignored
//    #endif
//
//    // Associate the DMA handle to the DCMI handle
//    __HAL_LINKDMA(&DCMIHandle, DMA_Handle, DMAHandle);
//
//    // Initialize the DCMI
//    HAL_DCMI_DeInit(&DCMIHandle);
//    if (HAL_DCMI_Init(&DCMIHandle) != HAL_OK) {
//        // Initialization Error
//        return -1;
//    }
//
//    // Configure and enable DCMI IRQ Channel
//    NVIC_SetPriority(DCMI_IRQn, IRQ_PRI_DCMI);
//    HAL_NVIC_EnableIRQ(DCMI_IRQn);
    return 0;
}

static int dma_config()
{
	// TODO: uncomment
	// note: this is impelmented in the dcmi_init() from the cubemx (same definitions)
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

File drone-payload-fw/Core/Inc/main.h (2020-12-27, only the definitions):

#define PROJ_SHA			"0x53a63a68b7373bf06e1bc09205d579fdcc81de3e"
#define ATWINC_AP_IP_BYTE0	0xC0 /* 192 */
#define ATWINC_AP_IP_BYTE1	0xA8 /* 168 */
#define ATWINC_AP_IP_BYTE2	0x01 /* 1 */
#define ATWINC_AP_IP_BYTE3	0x01 /* 1 */
#define MAIN_WIFI_M2M_SERVER_PORT         (6666)
#define MAIN_WIFI_M2M_BUFFER_SIZE      1024 //SOCKET_BUFFER_MAX_LENGTH
#define MAIN_WLAN_SSID                 "WINC1500_AP" /* < SSID */
#define MAIN_WLAN_AUTH                 M2M_WIFI_SEC_OPEN /* < Security manner */
#define MAIN_WLAN_CHANNEL              (6) /* < Channel number */
#define LED_R_Pin GPIO_PIN_0
#define LED_R_GPIO_Port GPIOC
#define LED_G_Pin GPIO_PIN_1
#define LED_G_GPIO_Port GPIOC
#define LED_B_Pin GPIO_PIN_2
#define LED_B_GPIO_Port GPIOC
#define WIFI_CHIP_EN_Pin GPIO_PIN_5
#define WIFI_CHIP_EN_GPIO_Port GPIOA
#define SPI2_NSS_Pin GPIO_PIN_12
#define SPI2_NSS_GPIO_Port GPIOB
#define WIFI_RESET_N_Pin GPIO_PIN_12
#define WIFI_RESET_N_GPIO_Port GPIOD
#define WIFI_INT_N_Pin GPIO_PIN_13
#define WIFI_INT_N_GPIO_Port GPIOD
#define WIFI_INT_N_EXTI_IRQn EXTI15_10_IRQn
#define DCMI_PCLK_Pin GPIO_PIN_8
#define DCMI_PCLK_GPIO_Port GPIOA
#define DCMI_RESET_Pin GPIO_PIN_10
#define DCMI_RESET_GPIO_Port GPIOA
#define SD_CD_Pin GPIO_PIN_0
#define SD_CD_GPIO_Port GPIOD
#define DCMI_PWDN_Pin GPIO_PIN_7
#define DCMI_PWDN_GPIO_Port GPIOD

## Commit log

2020-12-05 Imu data is exported to csv file
2020-12-26 1. changing i2c2 definitions - 100kHz 2. displaying the frames delay on pyplot
2020-12-27 1. ground_station_main.py - merging SOs ROS additions 2. fixing winc include paths - for linux compatibility 3. README.md updated
    [wifi_mngr.c]
2020-12-30 adding cad dir
    [OpenMV_rev_6_Camera_Bottom_cover.stl, OpenMV_rev_6_Camera_Top_cover.stl, OpenMV_rev_7_LCD_cover.stl]
2021-01-01 adding documents and datasheets
    [base.brd, base.sch]

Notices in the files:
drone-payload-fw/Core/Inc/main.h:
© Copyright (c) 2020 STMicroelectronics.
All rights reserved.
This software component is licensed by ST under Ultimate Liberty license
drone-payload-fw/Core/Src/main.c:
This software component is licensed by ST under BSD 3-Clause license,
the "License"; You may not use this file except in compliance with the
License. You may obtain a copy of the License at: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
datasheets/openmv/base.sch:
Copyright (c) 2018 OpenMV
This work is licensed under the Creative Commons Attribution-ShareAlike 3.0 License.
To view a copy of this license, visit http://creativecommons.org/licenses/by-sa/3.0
